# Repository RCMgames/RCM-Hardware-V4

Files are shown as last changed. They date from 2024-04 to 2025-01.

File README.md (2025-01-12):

# RCM-Hardware-V4

v1.3

* 4 motors and 7 servos OR 6 motors and 3 servos
* 3 additional input only pins
* 2 x 3 inches, 50.8 x 76.2 mm
* runs from 5 NiMH AA batteries OR 4.5-12v with the addition of voltage regulators (see list of components)
* [Qwiic](https://www.sparkfun.com/qwiic#faqs) connectors OR two more GPIO pins
* all components are hand-solderable through-hole parts except for the Qwiic connectors which are surface mount

Compatible with 38 pin devkitC ESP32 boards

program with [RCMv2](https://github.com/RCMgames/RCMv2)

### Alternatives
* An upgrade from [the original 3 versions of RCM boards](https://github.com/RCMgames/RCM_hardware_documentation_and_user_guide)

* Here are smaller and more powerful RCM boards: [BYTE](https://github.com/RCMgames/RCM-Hardware-BYTE) and [Nibble](https://github.com/RCMgames/RCM-Hardware-Nibble)

## Options for purchasing

* [PCBWay link](https://www.pcbway.com/project/shareproject/W454600ASI60_gerbers_RCM_Hardware_V4_v1_3_38d50617.html) (PCBWay will give me a commission without increasing the price for you). (approximately $5 for 5 boards and manufacturing takes 1-7 days).
* send the gerbers to a PCB manufacturer of your choice (details you may be asked for: min hole: 0.3mm, min track/spacing 6/6mil, 1 oz Cu outer)

## Components
Solder by hand to assemble your boards.
| part | links | quantity | notes |
| ----- | ----- | ----- | ----- |
| RCM V4 circuit board | see options for purchasing above | 1 | |
| ESP32 devkitC 38 pin | [digikey](https://www.digikey.com/en/products/detail/espressif-systems/ESP32-DEVKITC-32E/12091810) or find on Amazon | 1 | |
| L293D (or SN754410) | [digikey](https://www.digikey.com/en/products/detail/texas-instruments/L293DNE/379724) | 2 or 3 | |
| 16 pin IC socket | | 0 to 3 | depending on whether you solder the ICs directly and how many motors you want to use |
| 30k resistor | | 1 | |
| 10k resistor | | 1 | |
| 47uF capacitor | | 1 | |
| Qwiic connector (JST SH) | [digikey](https://www.digikey.com/en/products/detail/jst-sales-america-inc/SM04B-SRSS-TB/926710) | 0 to 2 | |
| 4 male header pins | | 1 | for I2C pins |
| 5 male header pins | | 1 | for extra input pins |
| 7 male header pins | | 4 | for servos |
| 4 female header pins | | 3 | for motors (can also use one 12 pin strip instead) |
| 19 female header pins | | 2 | for esp32 |
| battery wires | 2 male header pins OR JST RCY OR 9V battery snap | 1 | [Amazon JST RCY](https://www.amazon.com/dp/B00Z04QFN2/) |
| servo buck boost 5v 2A | [Pololu](https://www.pololu.com/product/4085) | 0 or 1 | if you want to supply voltages above or below what servos can accept (supplies other than 5AAs) |
| esp32 buck 5v 0.6A | [Pololu](https://www.pololu.com/product/3792) | 0 or 1 | if you want to supply voltages above 7 volts (supplies other than 5AAs) |

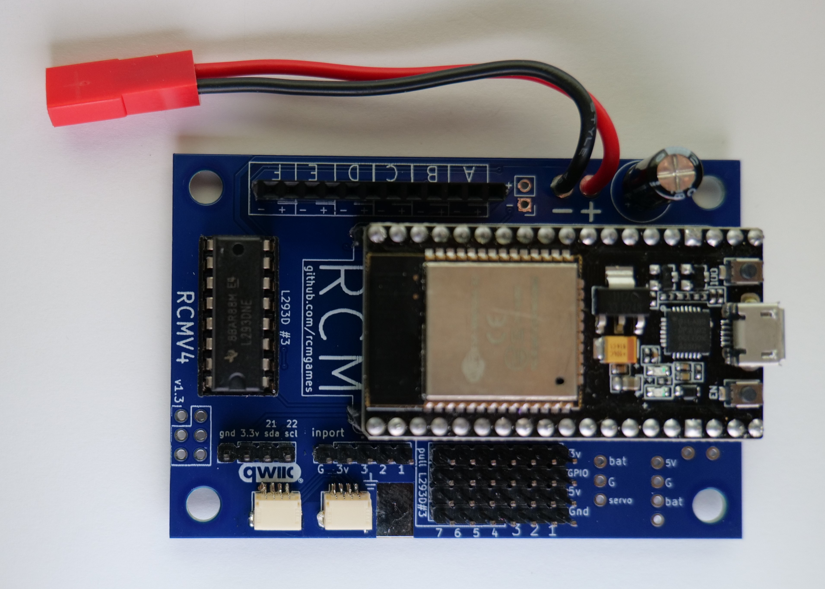
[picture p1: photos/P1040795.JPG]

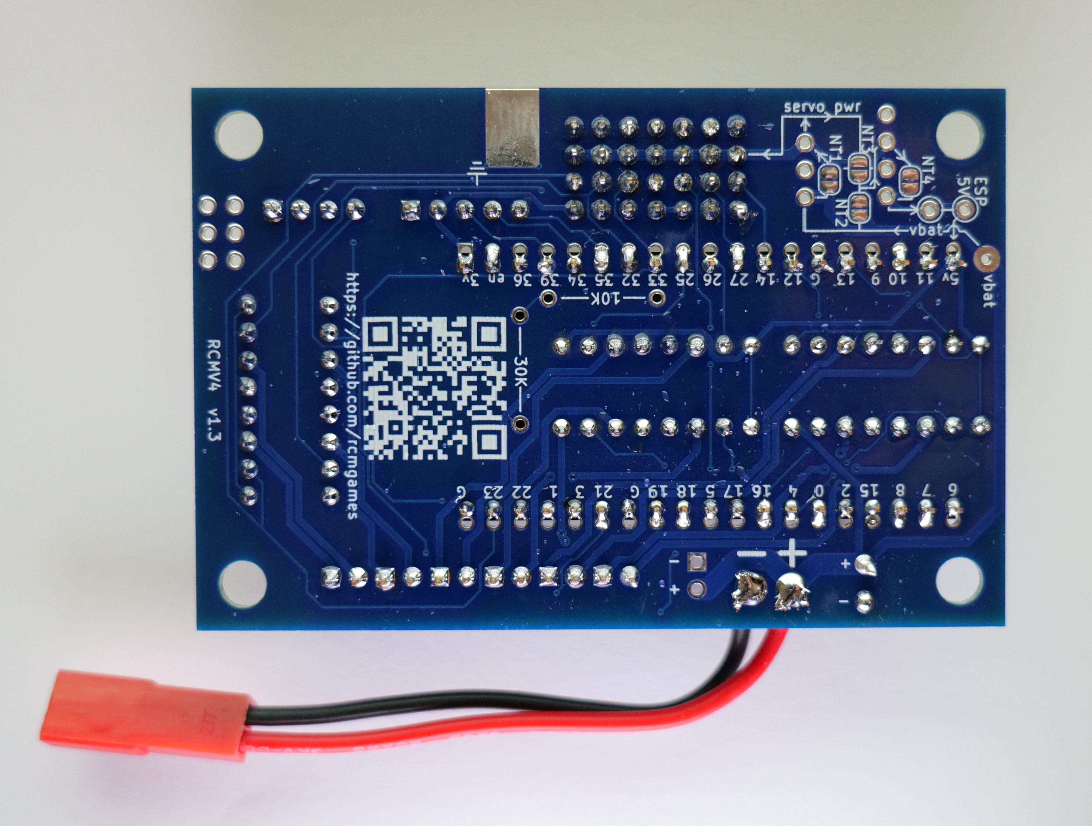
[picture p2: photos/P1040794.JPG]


The six pins at the bottom of the board near the QWIIC connectors are not connected to anything. They are meant to be used for soldering practice before adding components that matter.

## Acknowledgements
* I would like to thank [PCBWay](https://www.pcbway.com/) for sponsoring prototyping runs of this project. PCBWay produces very nice boards, supports open source hardware, and gave me great support as I worked on this project. Special thanks to Liam!

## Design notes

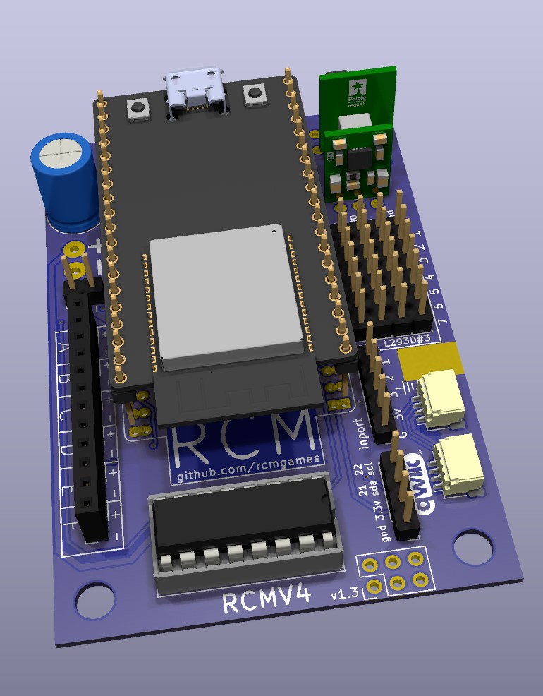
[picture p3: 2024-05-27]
CAD renders/render 1.jpg

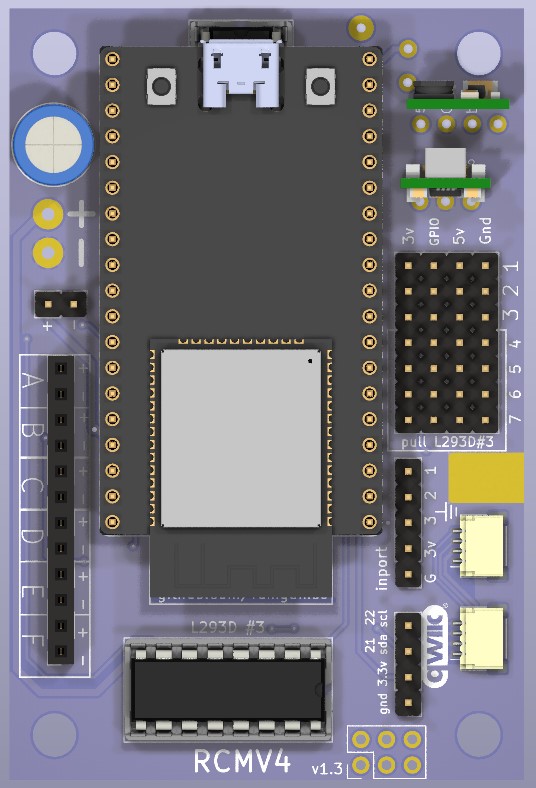
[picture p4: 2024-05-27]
CAD renders/top view.jpg

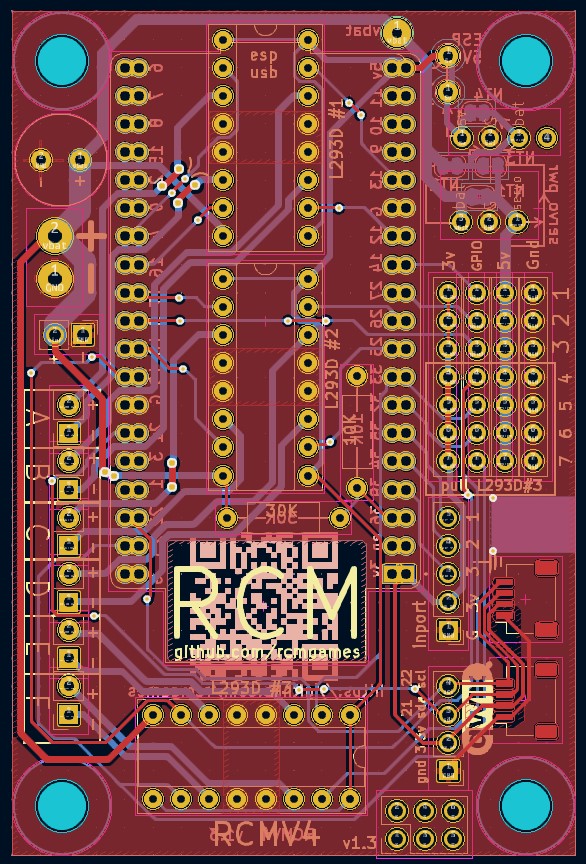
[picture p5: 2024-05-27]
CAD renders/kicad.jpg

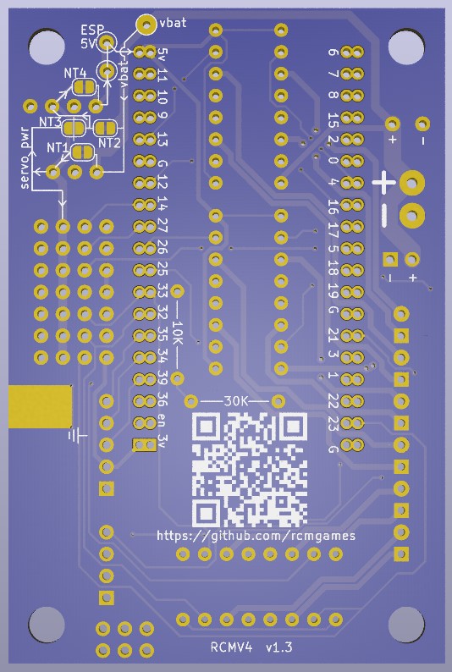
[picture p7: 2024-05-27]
CAD renders/bottom view.jpg

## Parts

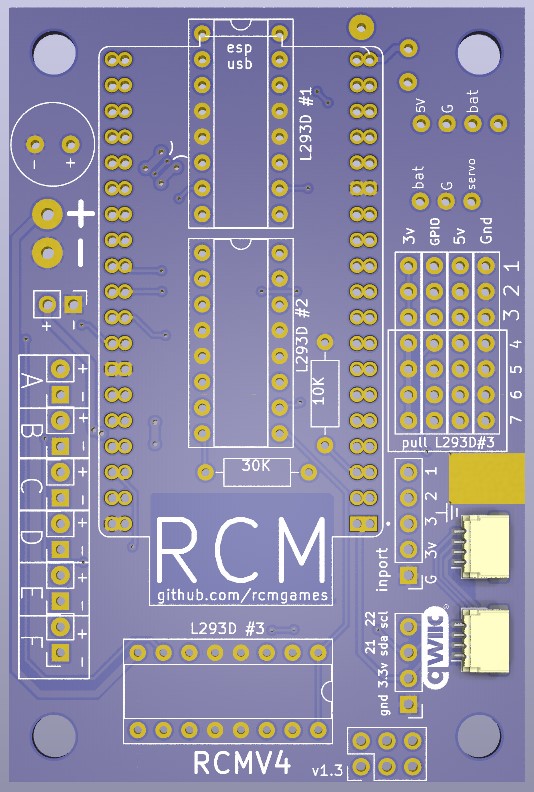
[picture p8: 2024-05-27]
CAD renders/top view no components.jpg

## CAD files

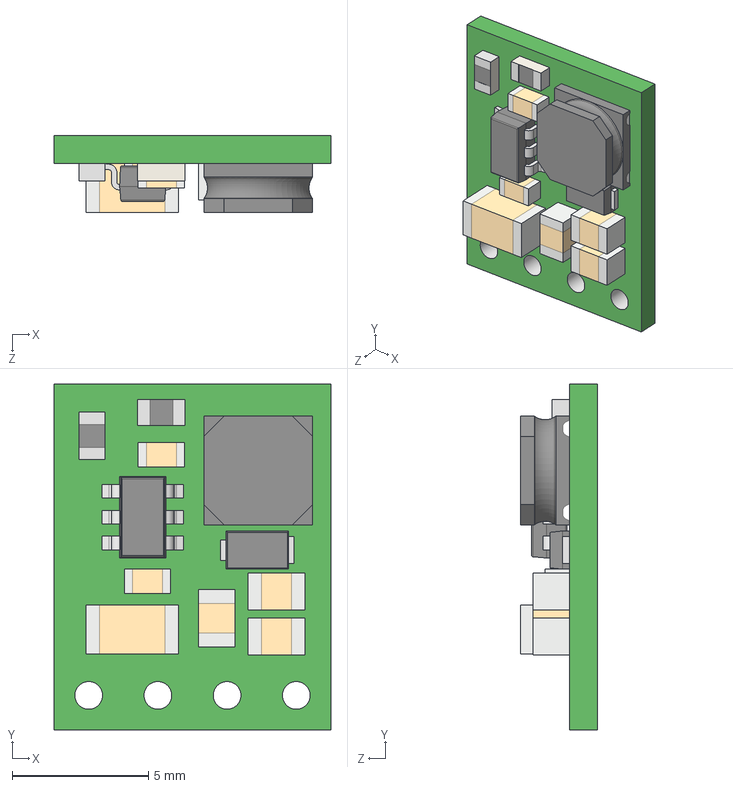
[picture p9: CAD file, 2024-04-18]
KICAD/footprints and symbols/step-down-voltage-regulator-d24v3fx-d24v6fx-d36v6fx.step
10.2 x 12.7 x 2.82 mm

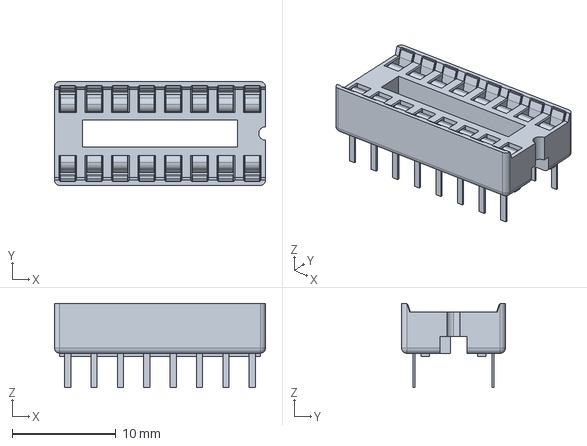
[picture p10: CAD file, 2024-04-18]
KICAD/footprints and symbols/1-2199298-4.stp
20.3 x 10.0 x 8.10 mm

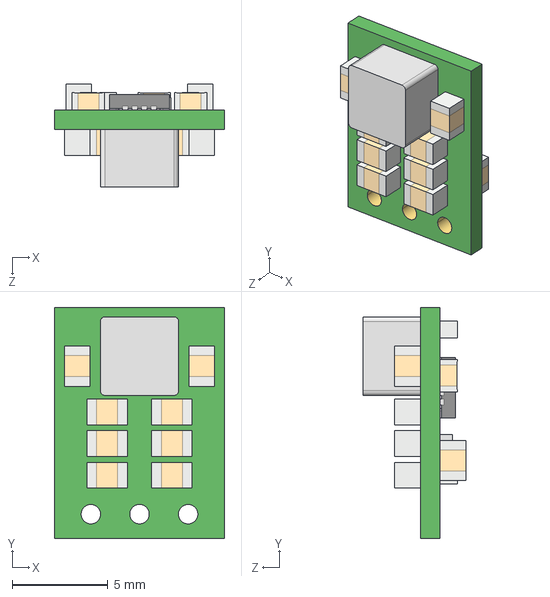
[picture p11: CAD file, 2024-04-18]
KICAD/footprints and symbols/pololu 4085 5v-2a-step-up-step-down-voltage-regulator-s13v20f5.step
8.89 x 12.1 x 5.37 mm

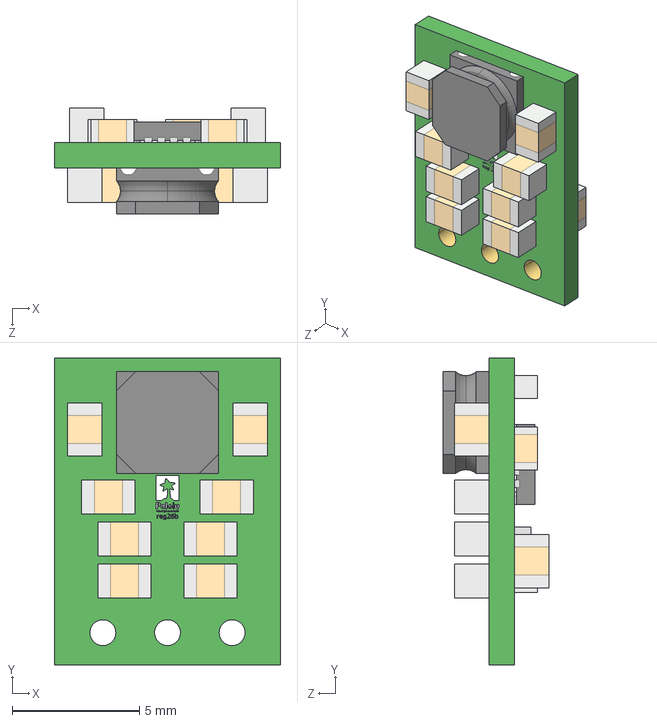
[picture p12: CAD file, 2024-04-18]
KICAD/footprints and symbols/pololu 4083 5v-1a-step-up-step-down-voltage-regulator-s13v10f5.step
8.89 x 12.1 x 4.17 mm

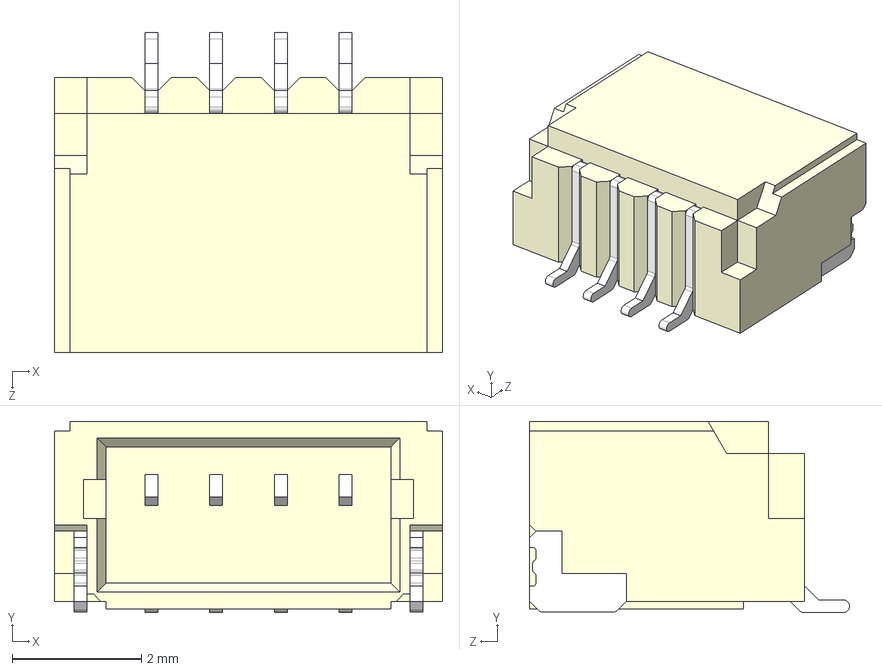
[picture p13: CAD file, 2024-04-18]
KICAD/footprints and symbols/SM04B-SRSS-TB(LF)(SN)--3DModel-STEP-269445.STEP
6.00 x 2.96 x 4.95 mm

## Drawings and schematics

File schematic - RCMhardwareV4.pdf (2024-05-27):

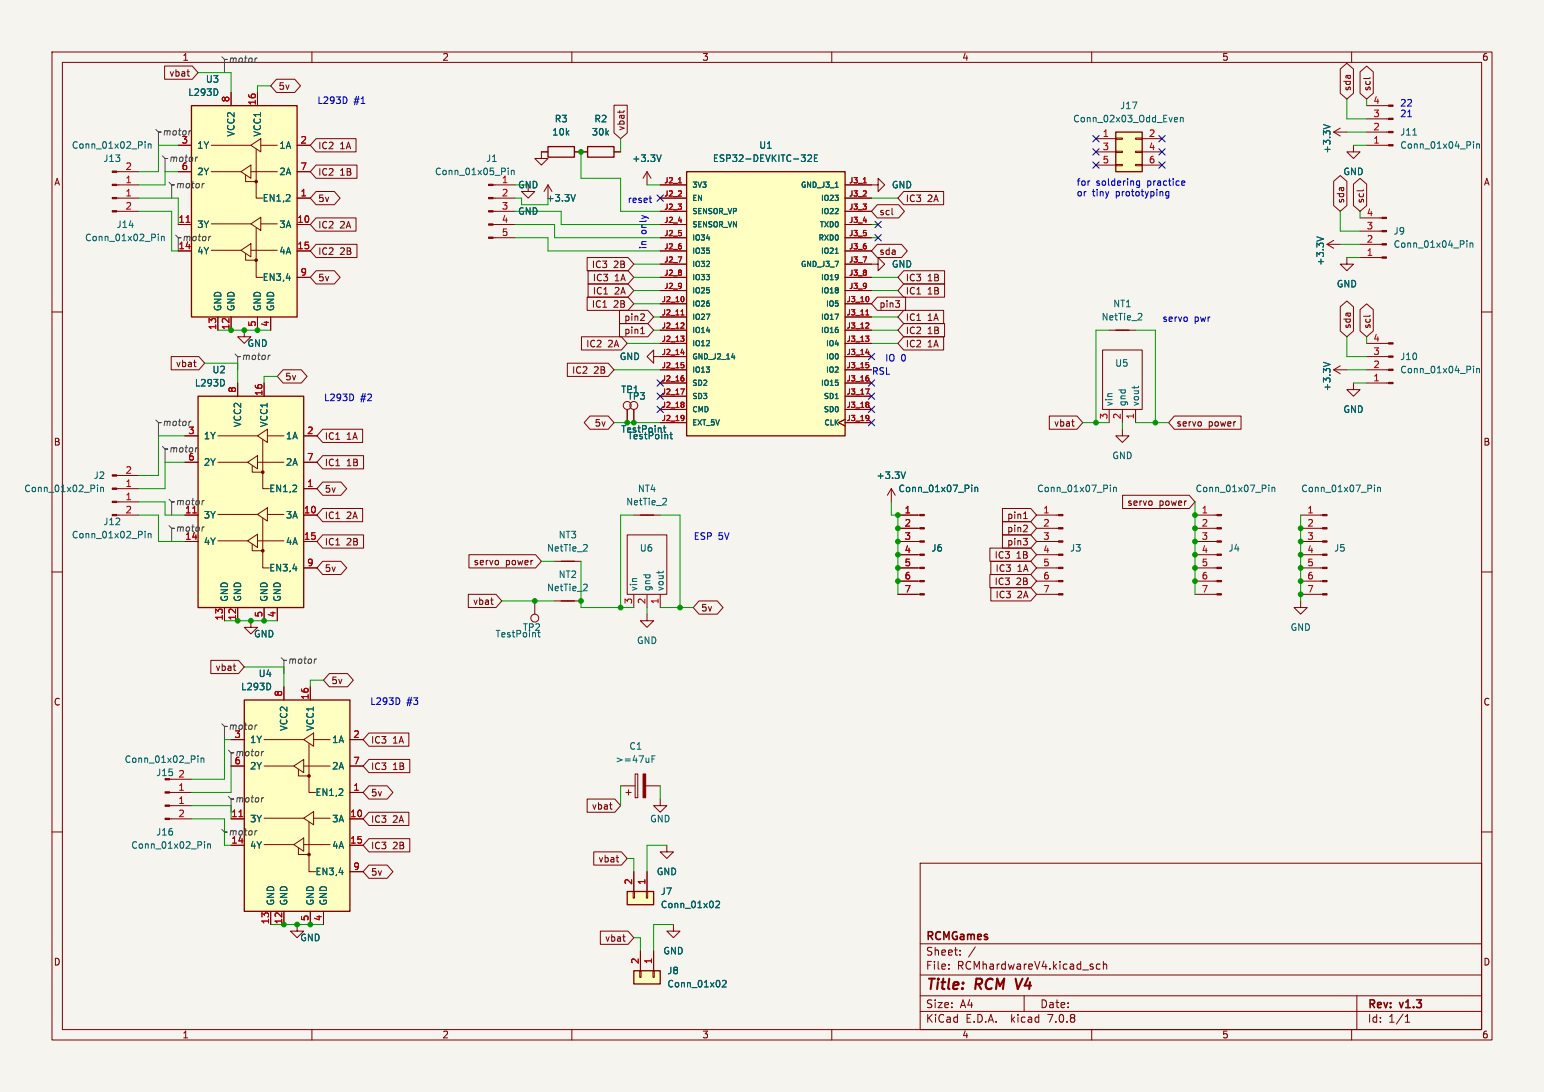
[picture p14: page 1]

vbat vbat servo power

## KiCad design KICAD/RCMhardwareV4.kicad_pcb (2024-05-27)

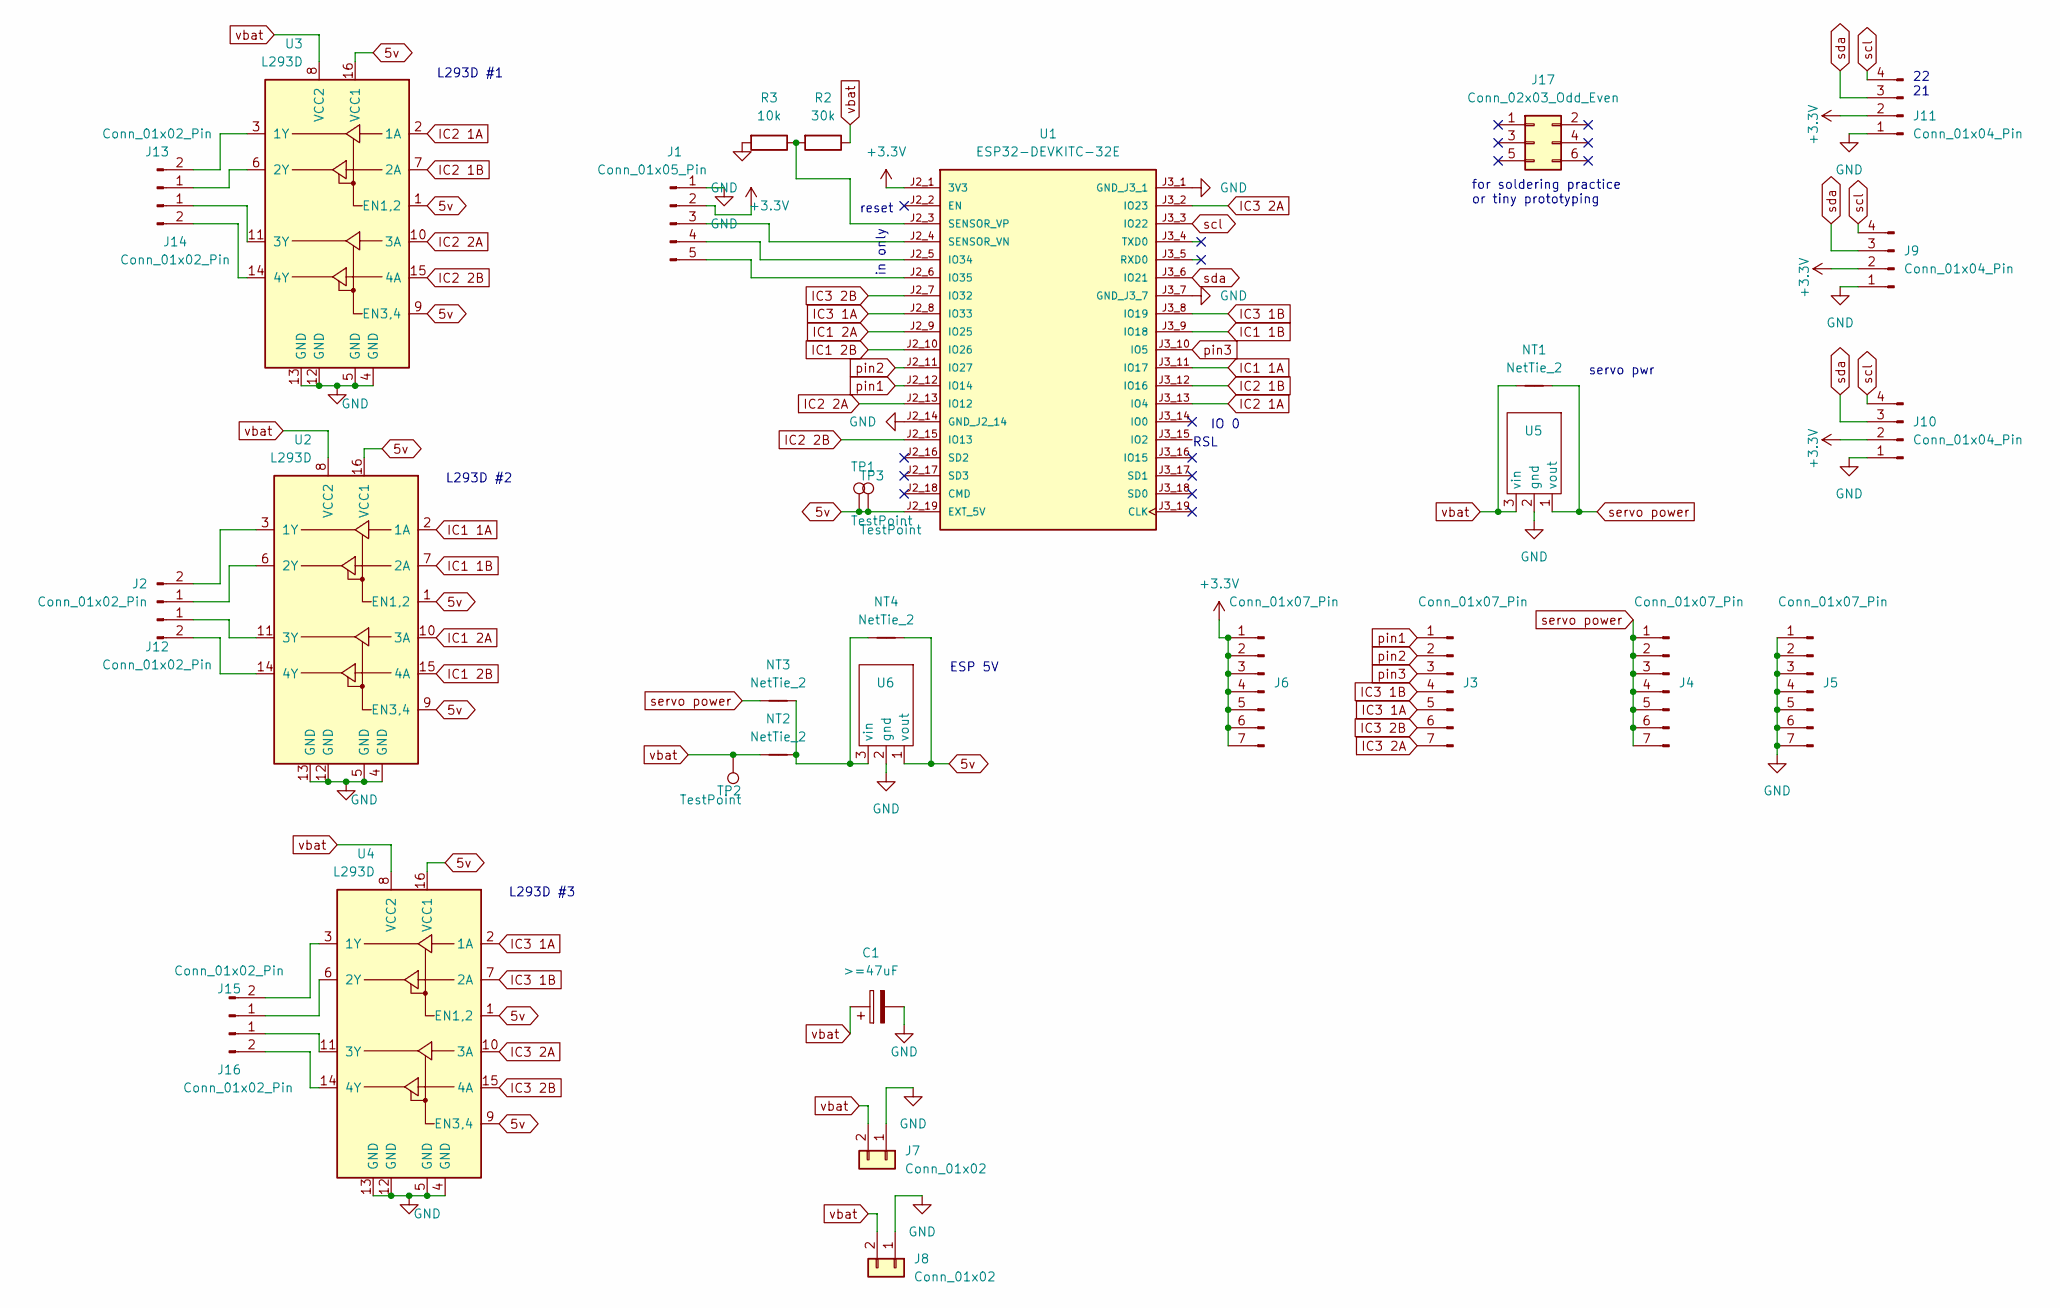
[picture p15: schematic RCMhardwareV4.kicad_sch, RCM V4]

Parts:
C1: >=47uF; C_Radial_D8.0mm_H11.5mm_P3.50mm
J1: Conn_01x05_Pin; PinHeader_1x05_P2.54mm_Vertical
J2, J12, J13, J14, J15, J16: Conn_01x02_Pin; PinSocket_1x02_P2.54mm_Vertical
J3, J4, J5, J6: Conn_01x07_Pin; PinHeader_1x07_P2.54mm_Vertical
J7: Conn_01x02; battery wires
J8: Conn_01x02; PinHeader_1x02_P2.54mm_Vertical
J9, J10: Conn_01x04_Pin; JST_SH_SM04B-SRSS-TB_1x04-1MP_P1.00mm_Horizontal
J11: Conn_01x04_Pin; PinHeader_1x04_P2.54mm_Vertical
J17: Conn_02x03_Odd_Even; PinHeader_2x03_P2.54mm_Vertical
NT1: NetTie_2; SolderJumper-2_P1.3mm_Bridged2Bar_RoundedPad1.0x1.5mm
NT2, NT4: NetTie_2; SolderJumper-2_P1.3mm_Bridged_RoundedPad1.0x1.5mm
NT3: NetTie_2; SolderJumper-2_P1.3mm_Open_RoundedPad1.0x1.5mm
R2: 30k; R_Axial_DIN0207_L6.3mm_D2.5mm_P10.16mm_Horizontal
R3: 10k; R_Axial_DIN0207_L6.3mm_D2.5mm_P10.16mm_Horizontal
TP1, TP2, TP3: TestPoint; TestPoint_THTPad_D2.0mm_Drill1.0mm
U1: ESP32-DEVKITC-32E; MODULE_ESP32-DEVKITC-32E
U2, U3, U4: L293D; DIP-16_W7.62mm_Socket
U5: pololu4085
U6: pololu3792

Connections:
5v: NT4.2, TP1.1, TP3.1, U1.J2_19 (EXT_5V), U2.1 (EN1,2), U2.9 (EN3,4), U2.16 (VCC1), U3.1 (EN1,2), U3.9 (EN3,4), U3.16 (VCC1), U4.1 (EN1,2), U4.9 (EN3,4), U4.16 (VCC1), U6.1 (vout)
+3.3V: J1.2, J6.1, J6.2, J6.3, J6.4, J6.5, J6.6, J6.7, J9.2, J10.2, J11.2, U1.J2_1 (3V3)
GND: C1.2, J1.1, J5.1, J5.2, J5.3, J5.4, J5.5, J5.6, J5.7, J7.1, J8.1, J9.1, J10.1, J11.1, R3.2, U1.J2_14 (GND_J2_14), U1.J3_1 (GND_J3_1), U1.J3_7 (GND_J3_7), U2.4 (GND), U2.5 (GND), U2.12 (GND), U2.13 (GND), U3.4 (GND), U3.5 (GND), U3.12 (GND), U3.13 (GND), U4.4 (GND), U4.5 (GND), U4.12 (GND), U4.13 (GND), U5.2 (gnd), U6.2 (gnd)
IC1 1A: U1.J3_11 (IO17), U2.2 (1A)
IC1 1B: U1.J3_9 (IO18), U2.7 (2A)
IC1 2A: U1.J2_9 (IO25), U2.10 (3A)
IC1 2B: U1.J2_10 (IO26), U2.15 (4A)
IC2 1A: U1.J3_13 (IO4), U3.2 (1A)
IC2 1B: U1.J3_12 (IO16), U3.7 (2A)
IC2 2A: U1.J2_13 (IO12), U3.10 (3A)
IC2 2B: U1.J2_15 (IO13), U3.15 (4A)
IC3 1A: J3.5, U1.J2_8 (IO33), U4.2 (1A)
IC3 1B: J3.4, U1.J3_8 (IO19), U4.7 (2A)
IC3 2A: J3.7, U1.J3_2 (IO23), U4.10 (3A)
IC3 2B: J3.6, U1.J2_7 (IO32), U4.15 (4A)
unnamed: J1.3, U1.J2_4 (SENSOR_VN)
unnamed: J1.4, U1.J2_5 (IO34)
unnamed: J1.5, U1.J2_6 (IO35)
unnamed: J2.1, U2.6 (2Y)
unnamed: J2.2, U2.3 (1Y)
unnamed: J12.1, U2.11 (3Y)
unnamed: J12.2, U2.14 (4Y)
unnamed: J13.1, U3.6 (2Y)
unnamed: J13.2, U3.3 (1Y)
unnamed: J14.1, U3.11 (3Y)
unnamed: J14.2, U3.14 (4Y)
unnamed: J15.1, U4.6 (2Y)
unnamed: J15.2, U4.3 (1Y)
unnamed: J16.1, U4.11 (3Y)
unnamed: J16.2, U4.14 (4Y)
unnamed: R2.2, R3.1, U1.J2_3 (SENSOR_VP)
unnamed: NT2.2, NT3.2, NT4.1, U6.3 (vin)
pin1: J3.1, U1.J2_12 (IO14)
pin2: J3.2, U1.J2_11 (IO27)
pin3: J3.3, U1.J3_10 (IO5)
scl: J9.4, J10.4, J11.4, U1.J3_3 (IO22)
sda: J9.3, J10.3, J11.3, U1.J3_6 (IO21)
servo power: J4.1, J4.2, J4.3, J4.4, J4.5, J4.6, J4.7, NT1.2, NT3.1, U5.1 (vout)
vbat: C1.1, J7.2, J8.2, NT1.1, NT2.1, R2.1, TP2.1, U2.8 (VCC2), U3.8 (VCC2), U4.8 (VCC2), U5.3 (vin)

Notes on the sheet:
in only
L293D #3
servo pwr
for soldering practice or tiny prototyping
RSL
L293D #2
22 21
ESP 5V
reset
L293D #1
IO 0

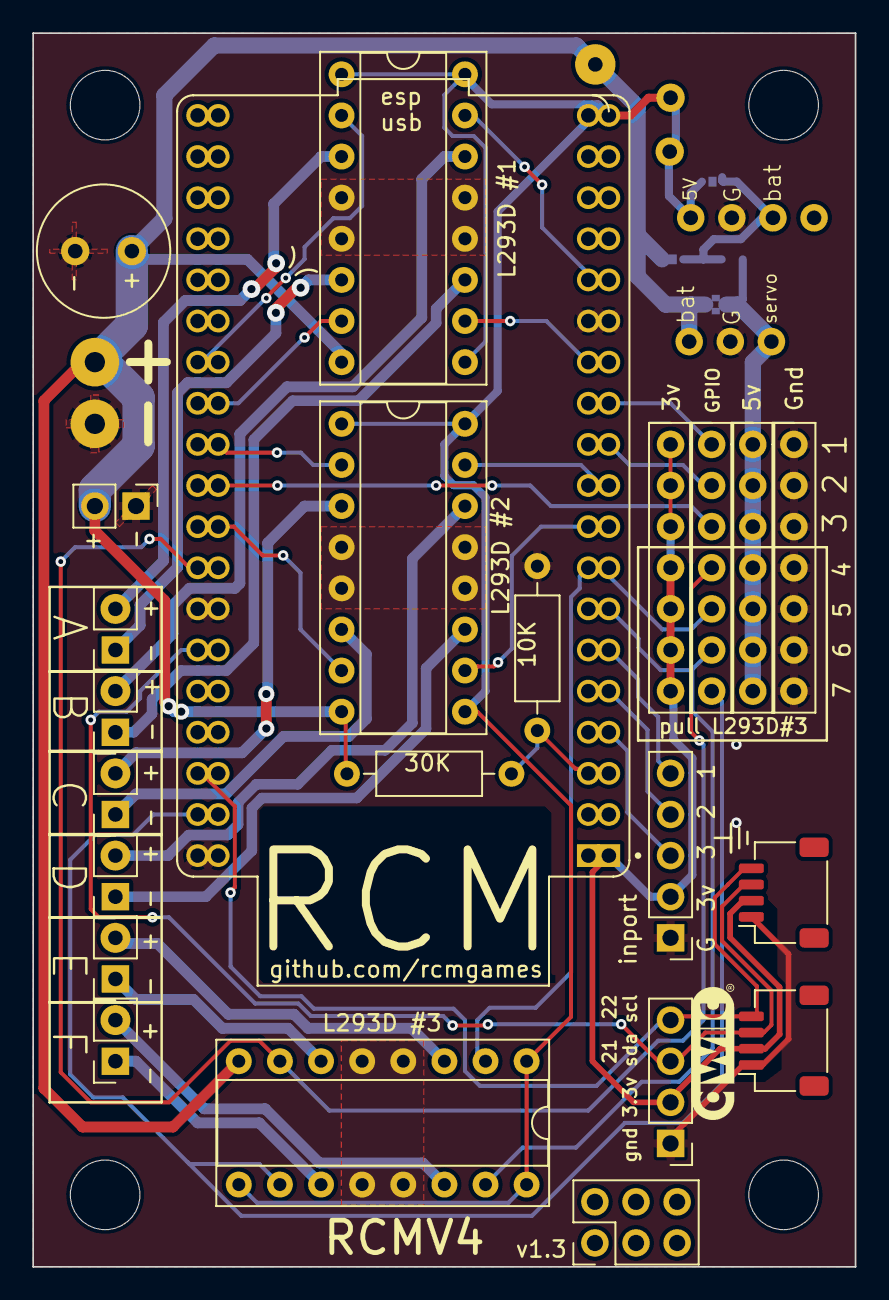
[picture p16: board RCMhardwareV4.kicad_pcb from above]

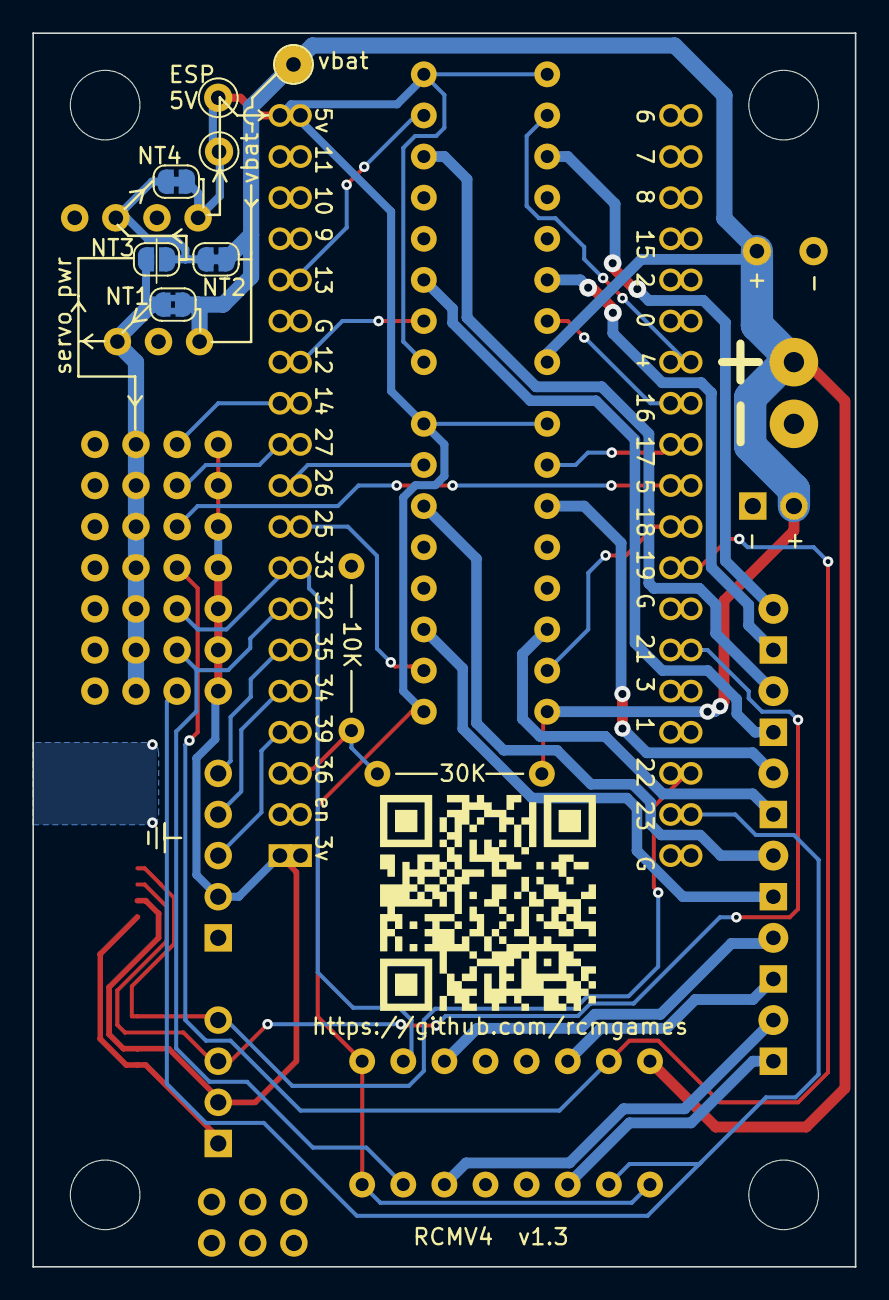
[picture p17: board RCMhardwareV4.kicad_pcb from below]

Board: 2 copper layers, 50.8 x 76.2 mm, 37 parts (7 on the bottom side), 39 nets.

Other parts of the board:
H1, H2, H3, H4: MountingHole; MountingHole_4.3mm_M4

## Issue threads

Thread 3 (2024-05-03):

Change the footprint of the ESP32 to be 0.1 inches narrower

joshua-8, 2024-05-03:
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

The worst part is this is the second time I've made this mistake

Closed 2024-05-04.

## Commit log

2024-04-25 add cad render
2024-05-04 v1.2 close #3 #4 #5
    [RCMhardwareV4.kicad_pcb, RCMhardwareV4.kicad_sch]
